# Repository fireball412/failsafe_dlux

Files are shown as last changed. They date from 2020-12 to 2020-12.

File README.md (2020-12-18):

# failsafe_dlux
 Failsafe for Turnigy dlux 250A HV 14s 60v ESC

Issue: The ESC has a hold time of almost 3 seconds in case of PPM signal loss. The PPM signal loss may occur if RX power supply fails (or in case of reception issues without RX-failsafe).

Solution approach: The circuit is powered by the RX. The supply is decoupled by a schottky diode and buffered by a capacitor. In case of RX power failure the circuit sets the ESC to the predefined failsafe position (failsafe_pos). Power failure is detected by comparing the supply in front of the diode with the predefined limit (voltagelimit). 
Failsafe is also triggered if the last proper PPM signal is older than the predefined limit (delaylimit).

red LED: indicates if output signal is below or equal failsafe position (either due to corresponding input signal or activated failsafe)
Blink code: 1 blink = PPM signal loss occurred at least once, 2 blínks = supply voltage was below limit at least once

demonstration:
https://www.youtube.com/watch?v=K2Zalw2rsIU

old version history

V.0.9: 
- first try

V.1.0: 
- first stable version
- improved software structure
- blink code for errors
- solution for delay control that was challenged by interrupt 

V.1.0.1:
- adapted for nano_RC_hold_V1.0 PCBs (pin number for input and output); no change needed for nano_RC_hold_V1.1 PCBs

V.1.0.2:
- using map function to scale ADC voltage to input voltage
- implementation 10k/68k voltage divider for 8.4V input voltage
- implementation of pistole grip stick conversion (pistol grip transmitter rest in neutral position, many ESC require -100% signal to stop)

2020/12/18 moved to github

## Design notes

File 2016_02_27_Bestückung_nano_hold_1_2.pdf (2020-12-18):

Part | Value | Device | Package | Description | Link
A6 | NA | WIREPAD2,15/1,0 2,15/1,0 | Wire PAD connect wire on PCB
A7 | NA | WIREPAD2,15/1,0 2,15/1,0 | Wire PAD connect wire on PCB
ADXL | NA | MA08-1 | MA08-1 | PIN HEADER
C5 | 1500µF, 16V | C-EU050H075X075 C050H075X075CAPACITOR, European symbol http://www.voelkner.de/products/69635/Elko-Low-Esr-105-1500F-16V-10x30-RM5-rohs.html
C7 | NA | C-EUC0805 | C0805 | CAPACITOR, European symbol
D1 | SB140 | Diode | DO201-15 | DIODE | http://www.voelkner.de/products/527385/Diotec-Schottky-Diode-SB140-Gehaeuseart-DO-15-I-F-1-A-Sperrspannung-U-R-40-V.html
EXT | NA | MA04-1 | MA04-1 | PIN HEADER
I2C | NA | MA03-1 | MA03-1 | PIN HEADER
NANO | ARDUINO Nano eingelötet oder 2x16(15) Buchsenleiste ARDUINO_NANO2 ARDUINO_NANO2 Arduino Nano2 | http://www.ebay.de/itm/Nano-V3-0-Modul-mit-ATmega328P-5V-Board-16MHz-aufgebaut-Arduino-kompatibel-/252099053034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
Buchsenleiste für steckbare Arduinomontage | http://www.ebay.de/itm/Stk-5-x-BUCHSENLEISTE-HEADER-16-polig-2-54mm-Arduino-bauweise-style-A475-/252186069262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
R1 | 0Ohm | R-EU_R0805 R0805 | RESISTOR, European symbol http://www.ebay.de/itm/100-x-Widerstand-SMD-0805-0-Ohm-0R-0-125W-5-55-125-C-/321926315435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
R2 | 0Ohm | R-EU_R0805 R0805 | RESISTOR, European symbol http://www.ebay.de/itm/100-x-Widerstand-SMD-0805-0-Ohm-0R-0-125W-5-55-125-C-/321926315435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
R3 | 68k | R-EU_R0805 R0805 | RESISTOR, European symbol http://www.ebay.de/itm/100-x-Widerstand-Resistor-0-125W-SMD-0805-1-WERT-FREI-WAHLBAR-/321870858057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
R4 | 10k | R-EU_R0805 R0805 | RESISTOR, European symbol http://www.ebay.de/itm/100-x-Widerstand-Resistor-0-125W-SMD-0805-1-WERT-FREI-WAHLBAR-/321870858057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
R5 | NA | R-EU_R0805 R0805 | RESISTOR, European symbol
R6 | NA | R-EU_R0805 R0805 | RESISTOR, European symbol
R7 | 0Ohm | R-EU_R0805 R0805 | RESISTOR, European symbol http://www.ebay.de/itm/100-x-Widerstand-SMD-0805-0-Ohm-0R-0-125W-5-55-125-C-/321926315435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
R8 | NA | R-EU_R0805 R0805 | RESISTOR, European symbol
R19 | NA | R-EU_R0805 R0805 | RESISTOR, European symbol
R20 | NA | R-EU_R0805 R0805 | RESISTOR, European symbol
SV1_IN | Stecker gewinkelt | MA03-1 | MA03-1 | PIN HEADER | http://www.ebay.de/itm/2-x-Stiftleiste-40-pol-rm-2-54-90-Grad-gewinkelt-brechbar-/301861218964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
SV1_OUT | Stecker gewinkelt | MA03-1 | MA03-1 | PIN HEADER | http://www.ebay.de/itm/2-x-Stiftleiste-40-pol-rm-2-54-90-Grad-gewinkelt-brechbar-/301861218964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
SV2_IN | NA | MA03-1 | MA03-1 | PIN HEADER
SV2_OUT | Stecker gewinkelt | MA03-1 | MA03-1 | PIN HEADER | http://www.ebay.de/itm/2-x-Stiftleiste-40-pol-rm-2-54-90-Grad-gewinkelt-brechbar-/301861218964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

http://www.voelkner.de/products/69635/Elko-Low-Esr-105-1500F-16V-10x30-RM5-rohs.html

http://www.voelkner.de/products/527385/Diotec-Schottky-Diode-SB140-Gehaeuseart-DO-15-I-F-1-A-Sperrspannung-U-R-40-V.html

http://www.ebay.de/itm/Nano-V3-0-Modul-mit-ATmega328P-5V-Board-16MHz-aufgebaut-Arduino-kompatibel-/252099053034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

http://www.ebay.de/itm/100-x-Widerstand-SMD-0805-0-Ohm-0R-0-125W-5-55-125-C-/321926315435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

http://www.ebay.de/itm/2-x-Stiftleiste-40-pol-rm-2-54-90-Grad-gewinkelt-brechbar-/301861218964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

http://www.ebay.de/itm/2-x-Stiftleiste-40-pol-rm-2-54-90-Grad-gewinkelt-brechbar-/301861218964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

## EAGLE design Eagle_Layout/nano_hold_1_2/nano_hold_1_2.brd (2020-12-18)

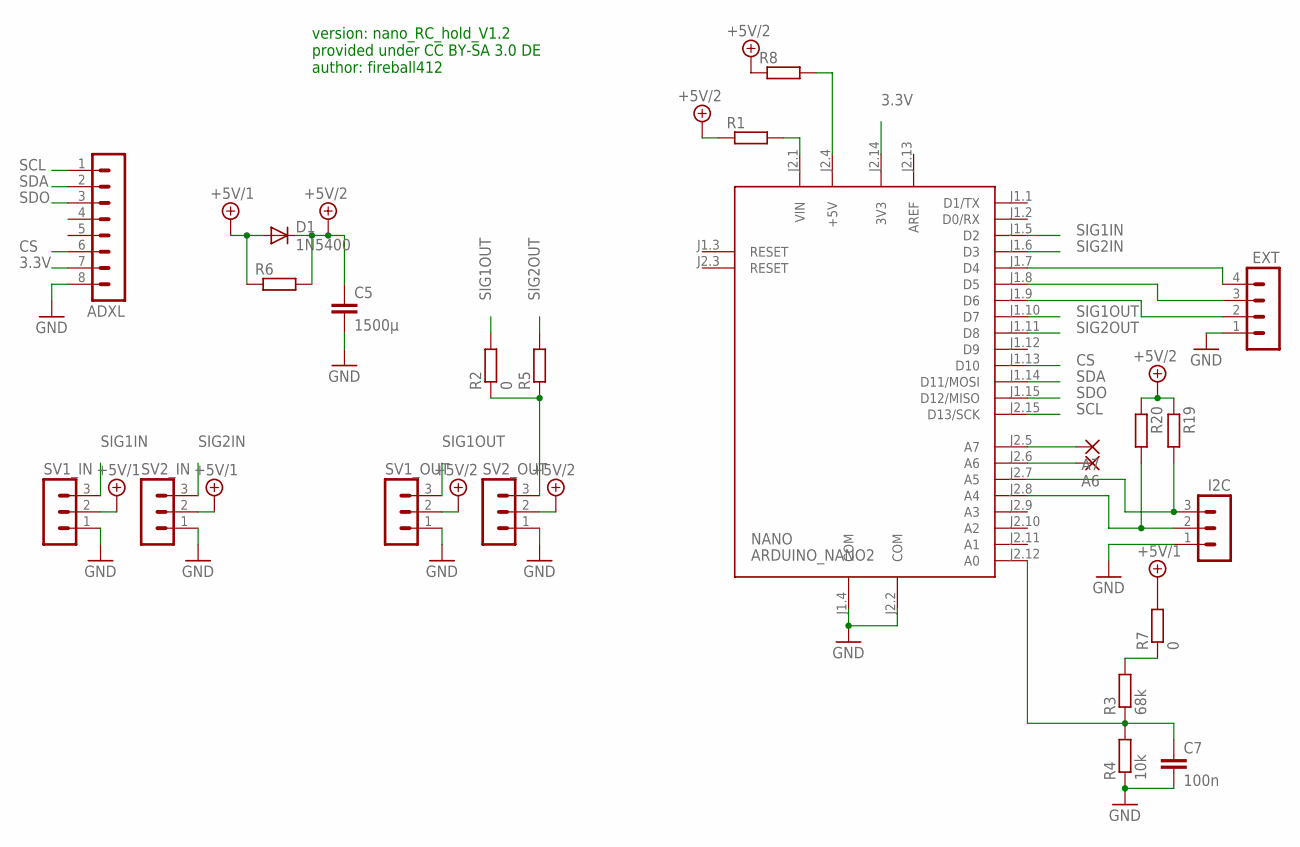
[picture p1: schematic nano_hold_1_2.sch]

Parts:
A6, A7: WIREPAD2,15/1,0; 2,15/1,0
ADXL: MA08-1
C5: 1500µ; C050H075X075
C7: 100n; C0805
D1: 1N5400; DO201-15
EXT: MA04-1
I2C: MA03-1
NANO: ARDUINO_NANO2
R1, R5, R6, R8, R19, R20: R-EU_R0805; R0805
R2, R7: 0; R0805
R3: 68k; R0805
R4: 10k; R0805
SV1_IN, SV1_OUT, SV2_IN, SV2_OUT: MA03-1

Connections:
3.3V: ADXL.7, NANO.J2.14 (3V3)
+5V/1: D1.A, R6.1, R7.2, SV1_IN.2, SV2_IN.2
+5V/2: C5.1, D1.C, R1.1, R6.2, R8.1, R19.1, R20.1, SV1_OUT.2, SV2_OUT.2
AREF: NANO.J2.13 (AREF)
CS: ADXL.6, NANO.J1.13 (D10)
GND: ADXL.8, C5.2, C7.2, EXT.1, I2C.1, NANO.J1.4 (COM), NANO.J2.2 (COM), R4.1, SV1_IN.1, SV1_OUT.1, SV2_IN.1, SV2_OUT.1
unnamed: NANO.J2.1 (VIN), R1.2
unnamed: C7.1, NANO.J2.12 (A0), R3.1, R4.2
unnamed: R2.1, R5.1, SV2_OUT.3
unnamed: EXT.4, NANO.J1.7 (D4)
unnamed: EXT.3, NANO.J1.8 (D5)
unnamed: NANO.J2.4 (+5V), R8.2
unnamed: EXT.2, NANO.J1.9 (D6)
unnamed: R3.2, R7.1
unnamed: A7.1, NANO.J2.5 (A7)
unnamed: A6.1, NANO.J2.6 (A6)
unnamed: I2C.3, NANO.J2.7 (A5), R19.2
unnamed: I2C.2, NANO.J2.8 (A4), R20.2
SCL: ADXL.1, NANO.J2.15 (D13/SCK)
SDA: ADXL.2, NANO.J1.14 (D11/MOSI)
SDO: ADXL.3, NANO.J1.15 (D12/MISO)
SIG1IN: NANO.J1.5 (D2), SV1_IN.3
SIG1OUT: NANO.J1.10 (D7), R2.2, SV1_OUT.3
SIG2IN: NANO.J1.6 (D3), SV2_IN.3
SIG2OUT: NANO.J1.11 (D8), R5.2

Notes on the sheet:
version: nano_RC_hold_V1.2 provided under CC BY-SA 3.0 DE author: fireball412

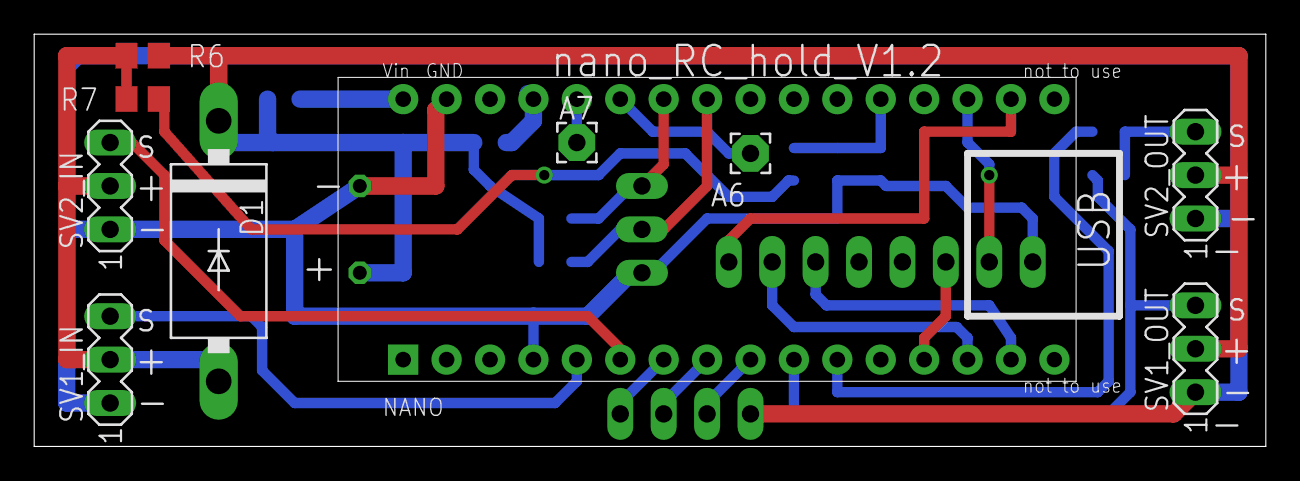
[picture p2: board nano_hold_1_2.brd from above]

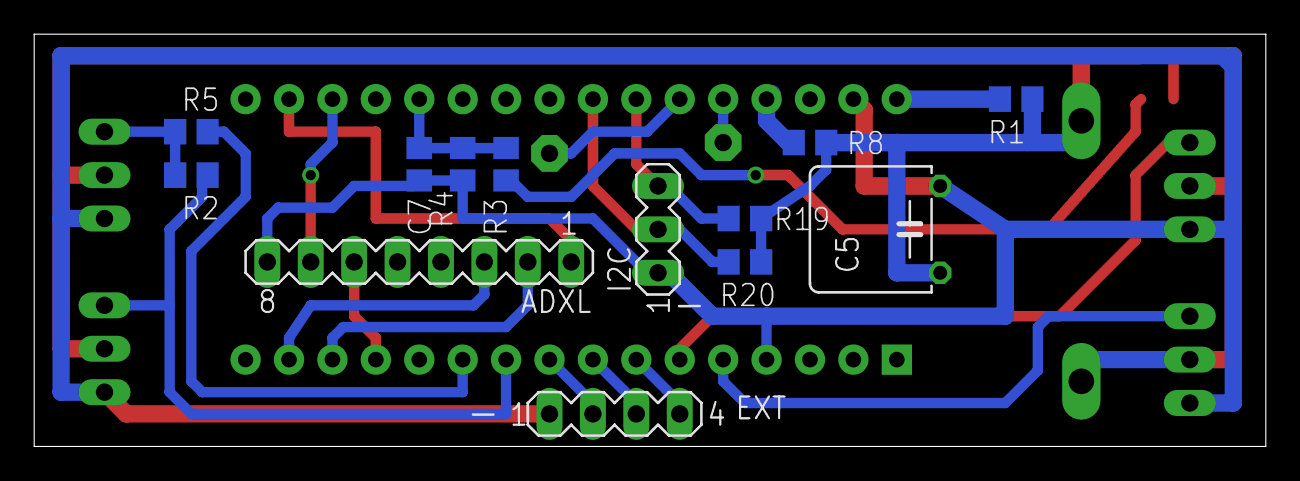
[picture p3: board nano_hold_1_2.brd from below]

Board: 2 copper layers, 72.1 x 24.1 mm, 23 parts (13 on the bottom side), 24 nets.

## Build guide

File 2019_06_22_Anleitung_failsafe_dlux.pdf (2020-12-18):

## Aufbauanleitung für failsafe_dlux

Autor: Stefan Leidich
Kontakt: fireball@t-online.de Version des Dokuments: V0.92

Features:

- Realisieren eines Failsafes für den dlux 250A HV Regler
- Reaktion auf Unterspannung und Signalverlust
- Senden des Stopp-Kommandos
- Eingangsspannung: 6,3-8,4V
- zwei parallele Reglerausgänge (Y-Kabel)
- Optional: Konvertierung des Eingangssignal von 0% bis +100% auf den Weg von -100% auf +100% für die Verwendung von Pistolensendern.
- https://www.youtube.com/watch?v=K2Zalw2rsIU

Disclaimer:

Die Hardware, die Software und die Dokumentation wurden mit großer Sorgfalt erstellt. Die Nutzung erfolgt auf eigenes Risiko. Die Veröffentlichung der Layouts erfolgt unter CC BY-SA 3.0 DE (https://creativecommons.org/licenses/by-sa/3.0/de/legalcode). Die Veröffentlich der Software unter GPLv3 (http://www.gnu.de/documents/gpl.de.html).

## 1. Beschaffung der Platine

Das Design der Platine wird als Eagle-Projekt zur Verfügung gestellt. Nahezu alle Leiterplatinenhersteller könne die *.brd Datei verarbeiten. Um das Board zu betrachten oder zu ändern ist die kostenlose Freeware-Version von eagle erforderlich:

http://www.cadsoft.de/download-eagle/eagle-freeware

Die Platine kann von jedem Hersteller gefertigt werden. Für die Bestellung der bestückten oder unbestückten Platine bei Bilex gibt es in Anlage A eine Musteremail.

## 2. Eingangskontrolle der Platine

Die Herstellung von Platinen erfolgt mit einer sehr geringen Fehlerquote. Dennoch sollte die Platine einer Sichtkontrolle unterzogen werden. Die Bauelemente sind in der Regel beschriftet. Der Bestückungsplan in Anlage B sollte als Vorlage verwendet werden.

## 3. Beschaffung des Arduino Nano

Der Arduino Nano sollte in der Version 3 (ATmega328P, 5V, 16MHz) beschafft werden. Andere Versionen wurden nicht getestet. Die Platinen sind zum Teil extrem günstig bei ebay zu bekommen. Den Nano gibt es komplett aufgebaut und mit beigelegter Stiftleiste zu kaufen. Wenn Löten absolut keine Option ist, sollte der komplett aufgebaut gekauft werden. Dieser kann in das Board mit Buchsenleiste gesteckt werden.

## 4. Inbetriebnahme des Arduino Nano

Die Inbetriebnahme erfordert ein Mini B-USB Kabel und die Arduino-Software:

https://www.arduino.cc/en/Main/Software

Die Installation der Software ist selbsterklärend. Nach erfolgreicher Installation gilt es folgende Auswahl zu treffen:

Werkzeuge -> Platine -> Arduino Nano

Werkzeuge -> Prozessor -> ATmega328

Es bietet sich an den zur Verfügung gestellten Programmcode (*.ino) in dieses Verzeichnis zu kopieren:

C:\Users\xxxx\Documents\Arduino

Der erste Funktionstest des Arduinos sollte noch außerhalb der Platine erfolgen. Dazu den Arduino an das USB-Kabel anschließen und mit dem Computer verbinden. Unter dem Menüpunkt:

Datei -> Beispiele -> 01.Basics -> Blink

findet man ein sehr einfaches Programm mit dem man die Grundfunktion testen kann. Die Übertragung des Programms in den Arduino erfolgt über:

Datei -> Hochladen

Danach sollte die LED "L" langsam blinken. Wer Interesse hat kann in der Zeile mit delay(1000) die Zahl ändern und so die Frequenz des Blinkens einstellen.

Wenn man den zur Verfügung gestellten Programmcode in oben genanntes Verzeichnis kopiert, finde man das Programm unter

Datei -> Sketchbooks-> xxx

Nach Lesen des Abschnitts 5 und ggf. notwendiger Anpassung der Software kann das Programm hochgeladen werden.

Der Arduino kann nach oder vor dem Programmieren auf die Platine gesteckt oder in diese eingelötet werden. Abbildung 1 zeigt das Layout. Die Orientierung des Arduino ist klar ersichtlich. Der USB Anschluss muss nach rechts zeigen. Aus fertigungstechnischen Gründen kann die Platine mit einer 16er-Buchsenleiste ausgestattet sein. Der Arduino hat jedoch nur 15 Pins. Es besteht somit die Gefahr, den Arduino falsch einzustecken bzw. einzulöten. Die nicht verwendeten Pins sind mit "not to use" beschriftet. Es ist somit klar, dass der Arduino linksbündig eingesteckt werden muss. Das falsche Einstecken kann zur permanenten Beschädigung führen.

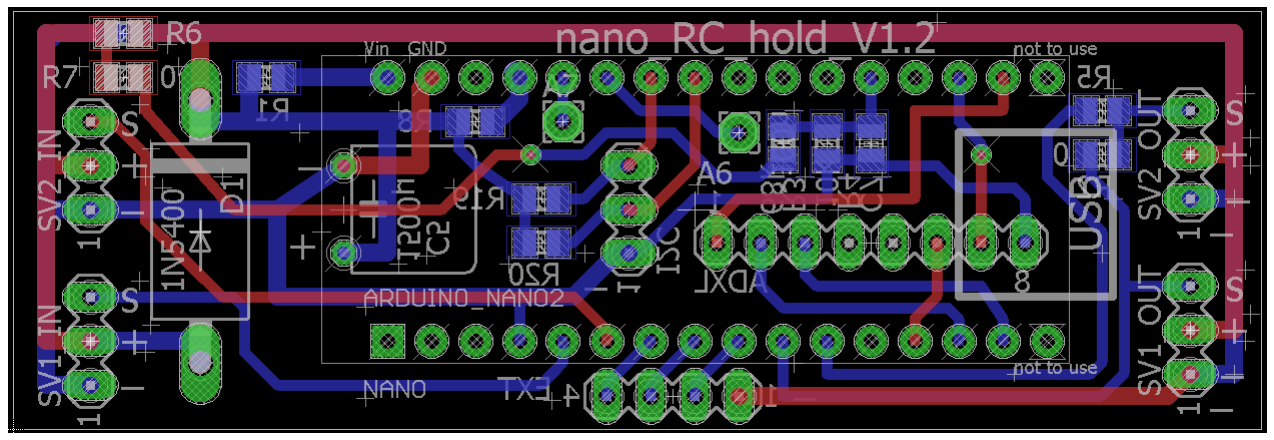
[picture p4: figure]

Abb. 1: Platinenlayout

## 5. Parametrisierung der Software

Die Software ist an verschiedene Anwendungsfälle anpassbar. Dies erfolgt über define Kommandos. Wenn die Zeile mit // beginnt, ist das Element nicht aktiv. Die Definitionen DEBUG, DEBUGFULL, DEBUGPPM und DEBUGVOL sollten nur erfahrene Programmierer verwenden. Jeder, der bei Durchsicht des Codes Fragen hat, wofür diese Kommandos gut sind, kann vermutlich auch nicht viel damit anfangen.

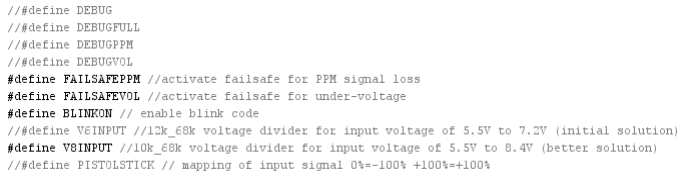
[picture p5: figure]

Listing A: Define Sektion

Definition FAILSAFEPPM

Mit dieser Definition wird der Failsafe für den Signalverlust definiert. Der Motor wird gestoppt, wenn das Modul für einen Zeitraum von mindestens 0,1s kein gültiges Signal empfangen. Die Zeitspanne wird durch diese Konstante in µs definiert:

Die Zeitspanne sollte nicht zu kurz gewählt werden. Es gilt zu beachten, dass er Empfänger nur alle 20ms ein Signal sendet.

Definition FAILSAFEVOL

Mit dieser Definition wird die Überwachung der Eingangsspannung aktiviert. Durch Auskommentierung (also // voranstellen) kann somit die Hauptfunktion des Moduls deaktiviert werden. Sinnvoll kann dies sein, wenn man das Modul nur für die Konvertierung des Gaswegs zur Verwendung einer Pistolensteuerung einsetzt. Die Spannungsschwelle wird mit dieser Konstanten definiert:

Die Schwelle von 4,5V hat sich bisher bewährt. Andere Werte sollten nur mit Vorsicht und mit ausreichend Sachverstand getestet werden.

Definition BLINKON

Die Definition BLINKON aktiviert den Blinkcode zur Anzeige von aufgetretenen Failsafe-Situationen während der Fahrt. Wenn die LED "L" im Ruhezustand bei einer Gasstellung oberhalb der Failsafe-Position (also -95% und höher) ein Mal blinkt, hat das Modul während der Laufzeit für einen bestimmten Zeitraum (siehe FAILSAFEPPM) kein gültiges Signal empfangen. Die Situation sollte nicht auftreten. Sie kann auftreten, wenn der Empfänger im Fall eines Empfangsverlustes kein Signal ausgibt (also kein Empfänger-Failsafe hat).

Wenn die rote LED zwei Mal blinkt, hat das Modul Unterspannung erkannt. Dies sollte man auch durch "stottern" des Motors gemerkt haben. Das Modul hätte dem Regler nämlich in diesem Fall zum Bremsen gezwungen. Eine mögliche Ursache für diesen Fall kann ein zu schwaches BEC sein. Wenn das Servo unter Last das BEC zum Einbrechen bringt, würde das Modul dies erkennen.

Definition V6INPUT, V8INPUT

Die Eingangsspannung wird vom Modul gemessen. Da der Arduino nicht ohne weiteres Spannungen oberhalb seiner eigenen Betriebsspannung messen kann, wird die Spannung durch R3 und R4 geteilt. Die erste Version der Hardware war für 6V Eingangsspannung ausgelegt. Der Spannungsteiler war mit 12k und 68k bestückt. Für den Betrieb bis 8,4V ist die Bestückung mit 10k und 68 erforderlich. Da der Arduino seine Außenbeschaltung nicht kennen kann, muss dies definiert werden. Es darf grundsätzlich nur eine der beiden Definitionen aktiv sein. Es gilt die für die Bestückung richtige zu wählen. (Die SMD-Widerstände sind beschriftet.)

Definition PISTOLSTICK

Mit dieser Definition wird die Konvertierung der Signalwege für Pistolenfernsteuerungen aktiviert. Pistolenfernsteuerung neutralisieren bei 0%. Viele Regler liefern dabei aber 50% Ausgangsleistung. Das Anlernen der Reglerwege ist oft nicht möglich. Die Funktion überträgt das Eingangssignal von 0% bis +100% auf den Weg von -100% bis +100%. Der Bremsbereich ist dann wirkungslos, da das Ausgangssignal -100% nicht unterschreiten kann. Die Definition der Mittenpositon erfolgt über diese Konstante:

Es ist sinnvoll mit der Gastrimmung den Zustand zu erreichen, dass in Neutralposition die rote LED "L" leuchtet. Wenn dies nicht der Fall ist, ist mehr Gasweg erforderlich, um das Anlaufen des Motors zu erreichen. Es gibt somit einen Todbereich.

Failsafe-Position

Die Failsafe-Postion beschreibt das Ausgangssignal im Fall des aktiven Failsafes. Der Wert kann über diese Konstante definiert werden:

Ein Wert von 1000(µs) entspricht ca. -125%. Test haben gezeigt, dass 1050(µs) besser sind, damit der Wert auch von jeder Fernsteuerung angefahren werden kann (in diesem Fall leuchtet die LED "L").

## 6. Inbetriebnahme des Gesamtsystems

Nach der Programmierung des Arduinos ist das System einsatzbereit. Das Modul wird linksseitig (SV1_IN) mit dem Empfänger verbunden (siehe Abb.2). Dafür ist ein Doppelbuchsen-Kabel erforderlich (oder Doppelstecker, je nach Verständnis von Stecker und Buchse). Der oder die Regler werden rechtsseitig verbunden (SV1_OUT, SV2_OUT). Für einen ersten Test bietet sich die Verwendung eines Servos an.

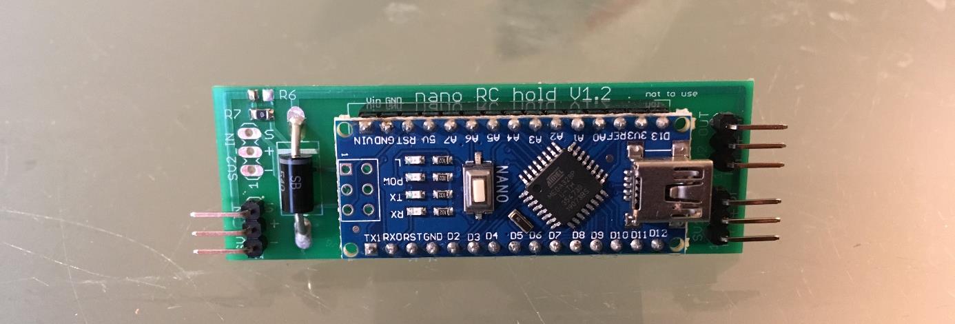
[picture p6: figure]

Abb. 2: Aufgebautes Modul

Wie in Abb. 2 ersichtlich sollte der Resettaster auf der Arduino-Platine entfernt werden. Es ist vorstellbar, dass der Taster durch Vibrationen im Betrieb gedrückt wird (Anschlagen an der Rumpfwand). Im Fall eines Resets wird für mehr als 1 Sekunde kein gültiges Signal ausgegeben. Der Motor läuft in diesem Fall weiter. Der Taster kann ohne Nachteile mit dem Lötkolben entfernt werden.

Es ist zum empfehlen die Platine mit WET.PROTECT zu imprägnieren und aufgrund der offen liegenden Leiter einzuschrumpfen. Die Montage im Boot sollte vibrationsgedämpft und nicht in unmittelbarer Nähe zum Empfänger bzw. zur Antenne des Empfängers (mit Telemetrie) platziert werden.

Die ordnungsgemäße Funktion sollte mit Hilfe des Prüfprotokolls aus Anhang C überprüft werden. Jede noch so kleine Abweichung vom erwarteten Verhalten sollte nicht ignoriert werden. Der Einfluss auf die Betriebssicherheit des Gesamtsystems ist nicht in jedem Fall vorhersehbar.

## Anlage A: Email für die Bestellung der Platine bei Bilex

Empfänger: info@bilex-lp.com

Betreff: Bestellung Platine nano_hold

Sehr geehrte Damen und Herren,

bitte erstellen Sie mir ein Angebot für die Herstellung und Bestückung von Leiterplatinen. Die Layoutdatei befindet sich im Anhang. Die gewünschte Bestückung* ist ebenfalls im Anhang zu finden.

Anzahl: N
Leiterplatinendicke: 1,55mm (FR4)
Art: 2-Lagig, durchkontaktiert Kupferdicke: 35µm
Größe: 72mmx24mm
Positionsdruck: Top
Lötstop: grün
Bearbeitung: gesägt
Bestückung nach Plan

Das Bauteil "NANO" sollte mit einer Buchsenleiste bestückt werden** Das Bauteil "NANO" sollte nicht bestückt werden**

Bestellerinformation:
Vorname Name
Strasse Hausnummer
PLZ Ort
Deutschland

* Wenn die Bestückung verändert wird, sollte dies im Text explizit erwähnt werden, um eventuelle Fehler zu vermeiden.
** Treffen einer Auswahl. Die Bestückung mit einer Buchsenleiste erlaubt das Einstecken des Arduino Nano. Das Einlöten ist dann aber nicht mehr möglich. Wenn der Arduino eingelötet wird, sollte die Platine nicht mit der Buchsenleiste bestückt werden.

## Anlage B: Bestückung

Die Excel-Version der Stückliste enthält Shop-Links

Part | Value | Device | Package | Description
A6 | NA | WIREPAD2,15/1,0 | 2,15/1,0 | Wire PAD connect wire on PCB
A7 | NA | WIREPAD2,15/1,0 | 2,15/1,0 | Wire PAD connect wire on PCB
ADXL | NA | MA08-1 | MA08-1 | PIN HEADER
C5 | 1500µF, 16V | C-EU050H075X075 | C050H075X075 | CAPACITOR, European symbol
C7 | NA | C-EUC0805 | C0805 | CAPACITOR, European symbol
D1 | SB140, (SB540) | Diode | DO201-15 | DIODE
EXT | NA | MA04-1 | MA04-1 | PIN HEADER
I2C | NA | MA03-1 | MA03-1 | PIN HEADER
NANO | ARDUINO Nano eingelötet oder 2x16(15) Buchsenleiste | ARDUINO_NANO2 | ARDUINO_NANO2 | Arduino Nano2
R1 | 0Ohm | R-EU_R0805 | R0805 | RESISTOR, European symbol
R2 | 0Ohm | R-EU_R0805 | R0805 | RESISTOR, European symbol
R3 | 68k | R-EU_R0805 | R0805 | RESISTOR, European symbol
R4 | 10k | R-EU_R0805 | R0805 | RESISTOR, European symbol
R5 | NA | R-EU_R0805 | R0805 | RESISTOR, European symbol
R6 | NA | R-EU_R0805 | R0805 | RESISTOR, European symbol
R7 | 0Ohm | R-EU_R0805 | R0805 | RESISTOR, European symbol
R8 | NA | R-EU_R0805 | R0805 | RESISTOR, European symbol
R19 | NA | R-EU_R0805 | R0805 | RESISTOR, European symbol
R20 | NA | R-EU_R0805 | R0805 | RESISTOR, European symbol
SV1_IN | Stecker gewinkelt | MA03-1 | MA03-1 | PIN HEADER
SV1_OUT | Stecker gewinkelt | MA03-1 | MA03-1 | PIN HEADER
SV2_IN | NA | MA03-1 | MA03-1 | PIN HEADER
SV2_OUT | Stecker gewinkelt | MA03-1 | MA03-1 | PIN HEADER

## Anlage C: Prüfprotokoll (beispielhaft ausgefüllt)

Test / Aktivität | Ergebnis | Bearbeiter | Datum
Prüfen der Platinenversion und Bestückung Vergleichen mit Bestückungdplan | Nano_RC_hold _V1.2 | Fireball412 | 22.06.19
Sichtprüfung und Doku (Abb. C1/2) | | Fireball412 | 22.06.19
Aufspielen der aktuellen Software: failsafe_dlux_V_1_0_2.ino #define BLINKON #define FAILSAFEVOL #define FAILSAFEPPM #define V8INPUT | | Stromfresser | xx.05.19
Testaufbau nach Abb. C3 aufbauen | ok | Fireball412 | 22.06.19
Mit Servotester (ohne Servo oder mit HV Servo) an 8,4V für 30 Minuten betreiben | ok | Fireball412 | 22.06.19
Mit Servotester (an 6,5V) verbinden und Servofunktion an Out 1 und Out 2 prüfen | ok | Fireball412 | 22.06.19
Prüfen, ob die LED leuchtet, wenn die Failsafe-Position angefahren wird | ok | Fireball412 | 22.06.19
Mit Servotester (an 6,5V) verbinden und Signalloss (kurzzeitiges Trennen des Signalkabels, siehe Abb. C4) emulieren. Prüfen ob LED danach einmal blinkt. | ok | Fireball412 | 22.06.19
Mit Servotester (an 6,5V) verbinden und Unterspannung emulieren (durch langsames Spannung reduzieren). Spannungslimit notieren (Sollwert ~4,65V). Spannung auf 6,5V erhöhen und prüfen ob LED zweimal blinkt und die Servofunktion wieder gegeben ist. | 4,63V ok | Fireball412 | 22.06.19
Neustart durch Spannungsunterbrechung | ok | Fireball412 | 22.06.19
Mit Servotester (an 6,5V) verbinden und 1h laufen lassen. Prüfen, ob keine Failsafe-Situation aufgetreten ist (also LED blinkt nicht). | ok | Fireball412 | 22.06.19
Prüfen, ob nach 1h Testlauf Servorreaktion noch gegeben ist. | ok | Fireball412 | 22.06.19
Prüfen, ob nach 1h Testlauf die Unterspannungserkennung noch funktioniert (durch Spannungsreduzierung, siehe oben) | ok | Fireball412 | 22.06.19
Neustart durch Spannungsunterbrechung | ok | Fireball412 | 22.06.19
Prüfen auf Servoreaktion und nicht blinkende LED | ok | Fireball412 | 22.06.19
Funktionskontrolle im Modell (unter anderem bei laufendem Motor den Servostecker aus dem Empfänger ziehen; weitere Tests nach Situation)

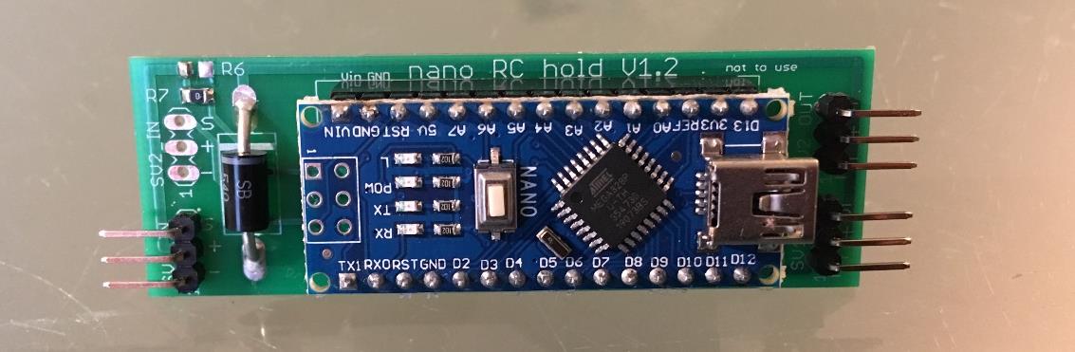
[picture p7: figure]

Abb. C1: Platinenoberseite

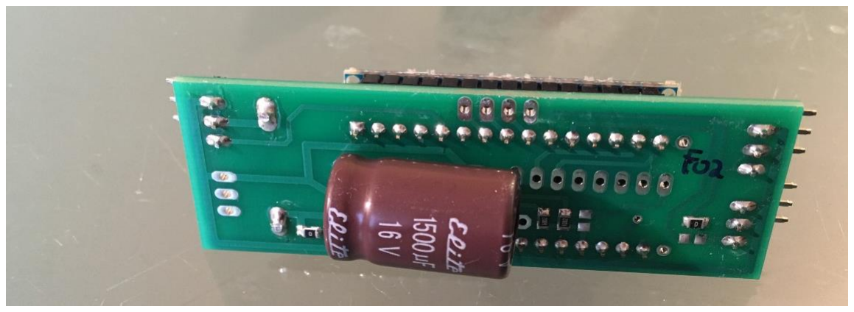
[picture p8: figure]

Abb. C2: Platinenunterseite

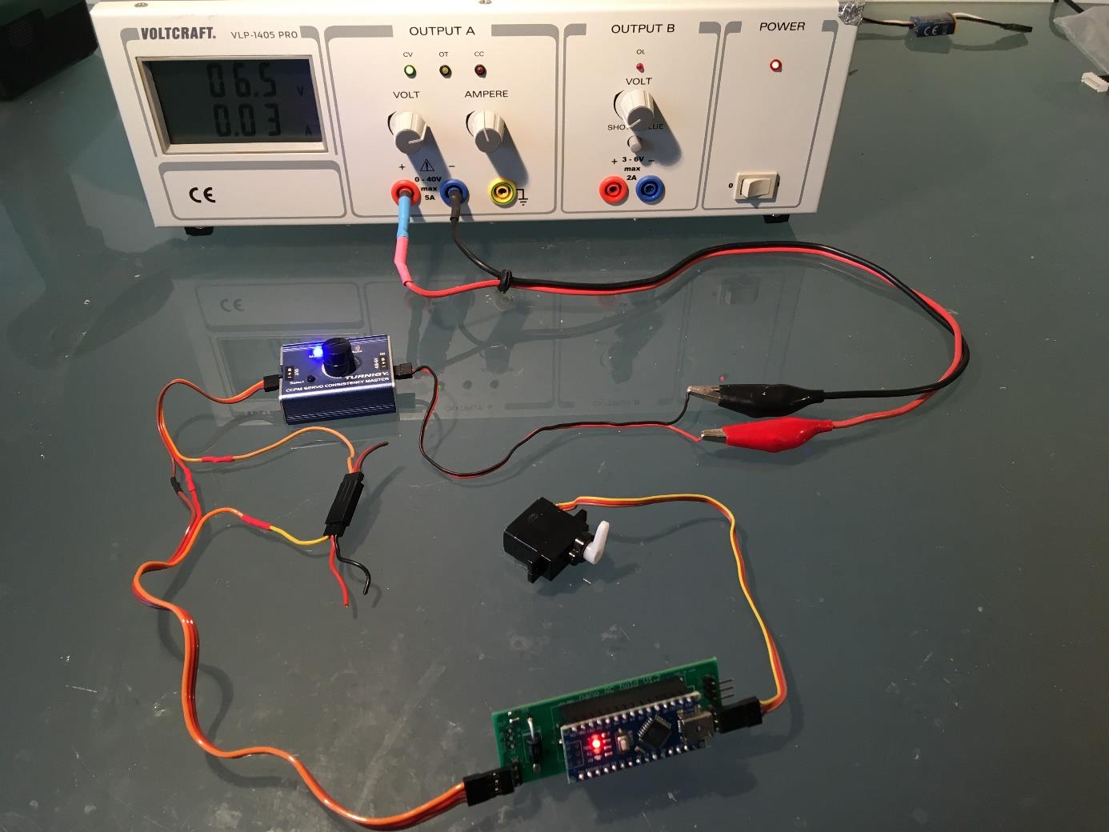
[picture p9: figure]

Abb. C3: Testaufbau

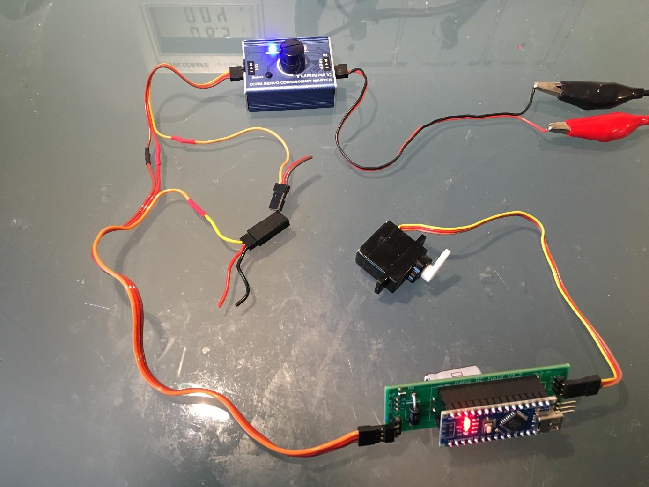
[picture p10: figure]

Abb. C4: Testaufbau (aufgetrenntes Signalkabel)

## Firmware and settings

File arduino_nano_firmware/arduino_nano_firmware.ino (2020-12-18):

/*
Board: "Arduino Nano"
Prozessor: ATmega328P (Old Bootloader)
 */

#include <Servo.h> 

//#define DEBUG
//#define DEBUGFULL
//#define DEBUGPPM
//#define DEBUGVOL
#define FAILSAFEPPM //activate failsafe for PPM signal loss
#define FAILSAFEVOL //activate failsafe for under-voltage
#define BLINKON // enable blink code
//#define V6INPUT //12k_68k voltage divider for input voltage of 5.5V to 7.2V (initial solution)
#define V8INPUT //10k_68k voltage divider for input voltage of 5.5V to 8.4V (better solution)
//#define PISTOLSTICK // mapping of input signal 0%=-100% +100%=+100%

Servo escout; 

const int servoch1inPin = 2;
const int servoch1outPin = 7;
const int sensorPin = A0; 
const int led_output=13;
const int voltagelimitdelay=5; //failsafe is activated if voltage measurement is 5 times below limit (~5*10ms=50ms delay)
const int ppmlossdelay=5; //failsafe is activated if ppm signal is not detected for more than 5 loops (~5*10ms=50ms delay)
const int maindelay=10; //delay of main loop in ms
const int rxreadydelay=1000; // wait for RX to get ready in ms
const int blinkinterval=50; // LED on time during blink as multiply of maindelay
const int blinkpause=200; // pause between blink series as multiply of maindelay
const int servo1min=1000; //limit of outputsignal
const int servo1max=2000; //limit of outputsignal
const int servoneutral=1500; //neutral postion of pistole transmitter
const int servo1validmin=800; //limit for plausibility, failsafe if beyond
const int servo1validmax=2200; //limit for plausibility, failsafe if beyond
const int voltagelimit=4500; //4500=4.5V threshold for faisafe

const int failsafe_pos=1050; //output position in case of failsafe

int servoout=failsafe_pos;
int voltagelimitdelaycounter=voltagelimitdelay; 
int ppmlossdelaycounter=ppmlossdelay;
int failsafewasactive=0;
int blinkcounter=blinkinterval;
int blinkstatus=0;
boolean redledstatus=false; 
boolean failsafeindicator=false;

const unsigned long delaylimit=100000; //100.000=0.1s failsafe in case of PPM signal loss
unsigned long delaymax=0;
unsigned long delaycurrent=0;
volatile unsigned long prev_time=0;
unsigned long prev_time_temp=0;
unsigned long micros_temp=0;
volatile unsigned long servoch1inraw=0;
int servoch1in=0;
long supplyvol=0;  

void setup() {
  analogReference(INTERNAL); //1.1V reference
  
  #ifdef DEBUG 
  //Initialize serial and wait for port to open:
  Serial.begin(9600); 
  while (!Serial) {
    ; // wait for serial port to connect. Needed for Leonardo only
  }
  #endif
  
  pinMode(servoch1inPin, INPUT_PULLUP); 
  pinMode(sensorPin, INPUT);
  pinMode(led_output, OUTPUT);
  // when pin D2 (=0) goes high, call the rising function
  attachInterrupt(0, rising, RISING);
  
  escout.attach(servoch1outPin);  // attaches the servo on pin XX to the servo object 
  escout.writeMicroseconds(failsafe_pos);              // outout set to failsafe position 
  digitalWrite(led_output,HIGH);
  delay(rxreadydelay);   //wait for RX to get ready
  digitalWrite(led_output,LOW);
}


void loop() {
  
  //skip invalid input reads
  if ((servoch1inraw <servo1validmin)||(servoch1inraw >servo1validmax))
  {
    servoch1in=failsafe_pos;
    }
    else
    {
      servoch1in=(int)servoch1inraw;
    }
   
 
 #ifdef PISTOLSTICK 
   servoch1in=map(servoch1in,servoneutral,servo1max,servo1min,servo1max);
 #endif
 
  //avoid PPM signal limits 
  if (servoch1in>=servo1max)
    {
    servoch1in=servo1max;
    }
    
  if (servoch1in<=servo1min)
    {
    servoch1in=servo1min;
    }
  
  servoout=servoch1in; //regular handover of ESC control signal
  
  supplyvol = analogRead(sensorPin); //read supply voltage
  
  #ifdef V6INPUT
    supplyvol = map(supplyvol, 0, 1023, 0, 7205); //correct for 12k/68k voltage divider
  //supplyvol*1100/1023*(655)/100; 
  #endif
  
  #ifdef V8INPUT 
    supplyvol = map(supplyvol, 0, 1023, 0, 8159); //correct for 10k/68k voltage divider
  #endif
  
  //voltage check
  if (supplyvol<=voltagelimit)
  {
    voltagelimitdelaycounter=voltagelimitdelaycounter-1; //voltage too low, decrease counter
  }
  else
 {
    voltagelimitdelaycounter=voltagelimitdelay; //single measurement of sufficient voltage resets counter
  }
  
    if (voltagelimitdelaycounter<=0) //if counter approaches zero then activate failsafe
  {
    voltagelimitdelaycounter=0;
    
    #ifdef FAILSAFEVOL
    servoout=failsafe_pos;
    failsafewasactive=2; //second kind of failsafe for blink code
    #endif
    
    #ifdef DEBUGVOL
    Serial.print("time: ");
    Serial.println(micros());
    Serial.print("Vol: ");
    Serial.println(supplyvol);
    #endif
   }
  
  
  prev_time_temp=prev_time; //to avoid overwrite by interrupt
  micros_temp=micros();
  delaycurrent=(unsigned long)(micros_temp-prev_time_temp);
  
  if (delaycurrent>delaymax)
  {
    delaymax=delaycurrent; //store max delay for debug purpose
  }
   
  //PPM check
  if (delaycurrent>=delaylimit)
  {
    ppmlossdelaycounter=ppmlossdelaycounter-1; //delay too low, decrease counter
  }
  else
 {
    ppmlossdelaycounter=ppmlossdelay; //single good PPM signal resets counter
  } 
        
  //PPM signal loss check
   if (ppmlossdelaycounter<=0)
  {
    ppmlossdelaycounter=0;
    
    #ifdef FAILSAFEPPM
    servoout=failsafe_pos;
    failsafewasactive=1; //first kind of failsafe for blink code
    #endif
    
    #ifdef DEBUGPPM
    Serial.print("time: ");
    Serial.println(micros());
    Serial.print("micros_temp: ");
    Serial.println(micros_temp);
    Serial.print("prev_time_temp: ");
    Serial.println(prev_time_temp);
    Serial.print("delaycurrent: ");
    Serial.println(delaycurrent);
    #endif
  }
  
  #ifdef DEBUGFULL
  //debug output servo position
  Serial.print("In raw: ");
  Serial.println(servoch1inraw);
  Serial.print("In: ");
  Serial.println(servoch1in);
  Serial.print("Out: ");
  Serial.println(servoout);
  Serial.print("Vol: ");
  Serial.println(supplyvol);
  Serial.print("delaymax: ");
  Serial.println(delaymax);
  #endif

  #ifdef BLINKON
  //realize blink code
  if (blinkstatus>0)
  {
     blinkcounter=blinkcounter-1;
     if (blinkcounter<=0)
      {
      blinkcounter=blinkinterval;
      redledstatus=!redledstatus;
      digitalWrite(led_output,redledstatus);
      blinkstatus=blinkstatus-1;
      }
  }
  else
  {
    blinkstatus=failsafewasactive*2;
    blinkcounter=blinkpause; //define pause between blink codes
  }
  
  //indicate failsafe position, overwrites blink code
   if (servoout<=failsafe_pos)
  {
    digitalWrite(led_output,HIGH);
    failsafeindicator=true;
  }
  else
  {
    if (failsafeindicator==true)
    {
        digitalWrite(led_output,LOW);
        failsafeindicator=false;
    }    
    
  }
  #endif
  
  //set ESC output
  escout.writeMicroseconds(servoout);          
   
  delay(maindelay);
}


void rising() {
  attachInterrupt(0, falling, FALLING);
  prev_time = micros();
  }
 
void falling() {
  attachInterrupt(0, rising, RISING);
  servoch1inraw = (unsigned long)(micros()-prev_time);
  }

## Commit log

2020-12-18 Create arduino_nano_firmware.ino
    append Arduino project
2020-12-18 adding files
    layout, ,manual, ...
    [nano_hold_1_2.brd, nano_hold_1_2.sch]
2020-12-27 Update arduino_nano_firmware.ino
    Some really important change :-)
2020-12-27 Update arduino_nano_firmware.ino
    redo change
